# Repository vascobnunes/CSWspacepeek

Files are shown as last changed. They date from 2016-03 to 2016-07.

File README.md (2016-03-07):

# CSWspacepeek

A ideia consiste em construir um balão atmosférico com uma payload que permita filmar toda a sequência de ascenção e queda do balão, com principal foco na obtenção de imagens da superfície terrestre a partir do limiar do espaço, tendo o logotipo da critical em primeiro plano. 
Como objectivos secundários, tentar-se-iam recolher medições telemétricas, atmosféricas e geográficas da viagem.

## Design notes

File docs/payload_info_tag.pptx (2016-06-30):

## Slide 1

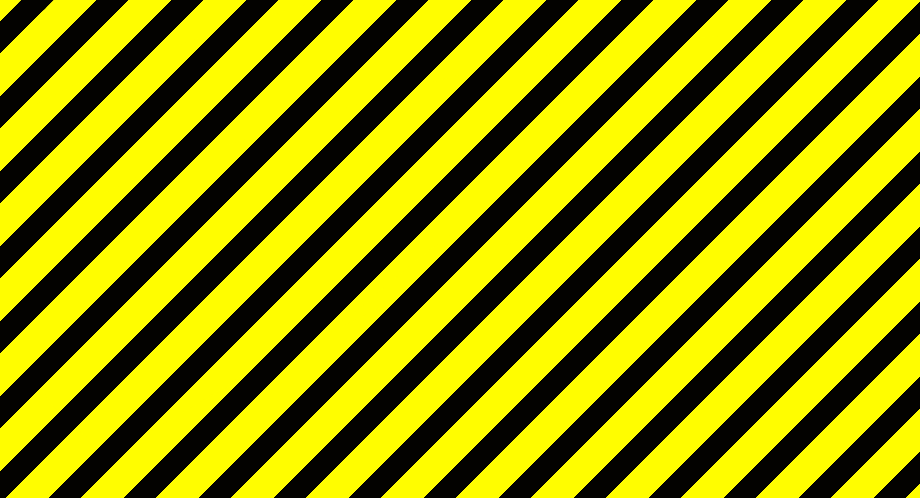
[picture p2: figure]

MEDIÇÕES METEOROLÓGICAS

SE ENCONTRAR POR FAVOR:
NÃO ABRA A CAIXA

CONTACTE:
spacepeek@gmail.com
+351 91 321 50 55
RECOMPENSA PELA DEVOLUÇÃO

CAIXA E CONTEÚDOS NÃO PERIGOSOS

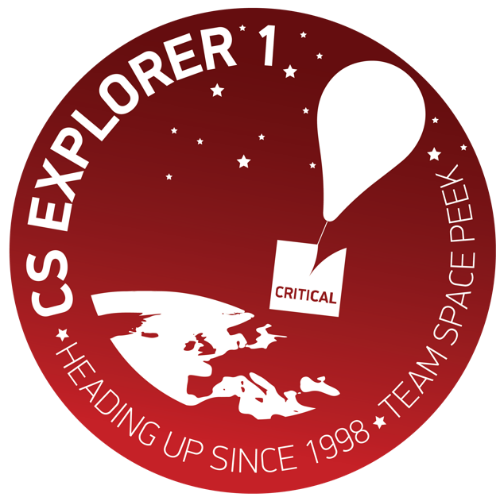
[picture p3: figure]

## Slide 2

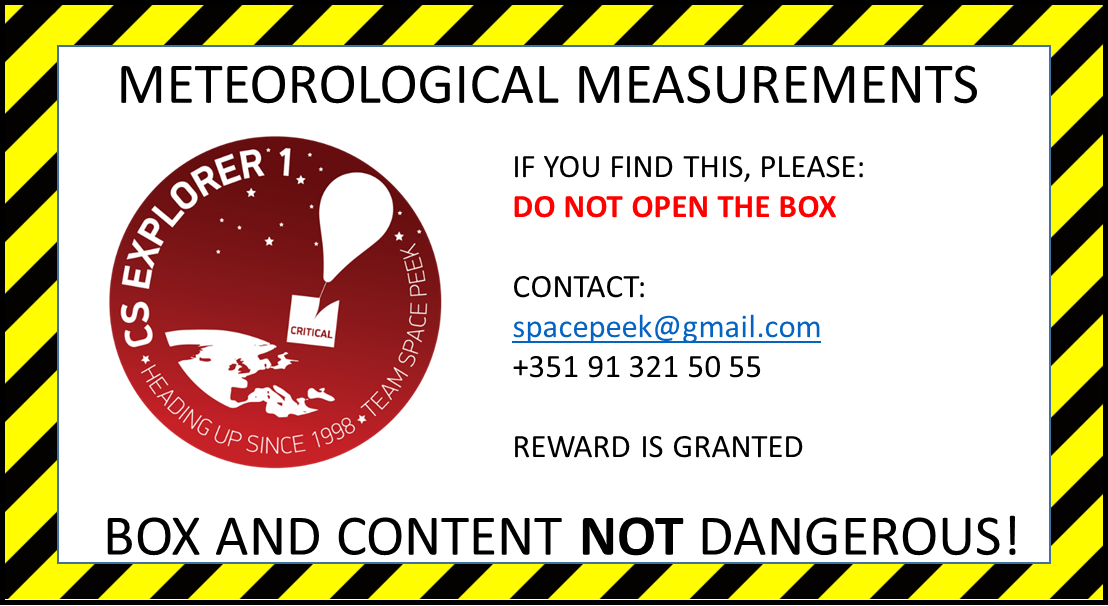
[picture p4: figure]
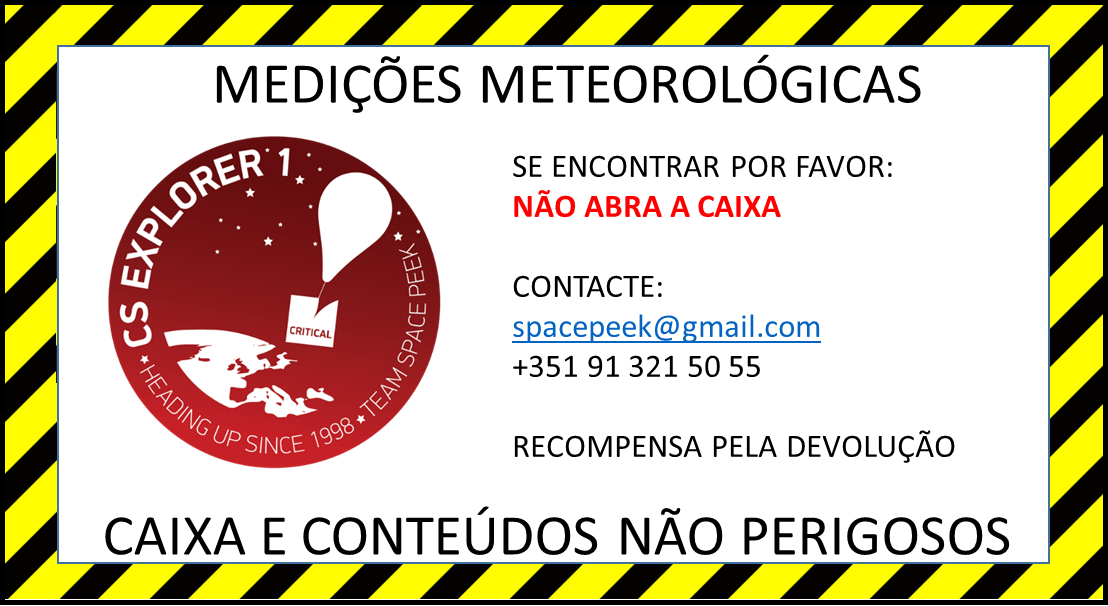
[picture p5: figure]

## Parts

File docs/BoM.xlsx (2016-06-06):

Category | Item # | Item Description | Amount | Provider / website | Unit Price | Total Price | Procurement priority | Notes for procurement
Flight hardware | ~~1~~ | ~~Balão testes (100g)~~ | ~~0~~ | ~~http://randomsolutions.co.uk/Random_Aerospace/Balloons.html~~ | ~~34.08 €~~ | ~~0.00 €~~ | Deprecated
 | 2 | Brand New, High Quality Balloon. 1000g Hwoyee HY-1000 (£46.95) | 1 | http://randomsolutions.co.uk/Random_Aerospace/Balloons.html | 59.67 € | 59.67 € | High | Items #2, #3, #26 and #27 can be ordered together
 | 3 | RocketMan Balloon Parachute - 3ft (£39.95) | 1 | http://randomsolutions.co.uk/Random_Aerospace/Parachutes.html | 50.78 € | 50.78 € | High | Items #2, #3, #26 and #27 can be ordered together
 | 26 | 1.0mm Braided Nylon Cord - Breaking strain approx. 22.5Kg (220N**). Weight approx. 0.6g per meter (£2.25) | 1 | http://randomsolutions.co.uk/Random_Aerospace/Stuff.html | 2.86 € | 2.86 € | High | Items #2, #3, #26 and #27 can be ordered together
 | 27 | 2.7L Polystyrene Payload Box (£7.95) | 1 | http://randomsolutions.co.uk/Random_Aerospace/Stuff.html | 10.11 € | 10.11 € | High | Items #2, #3, #26 and #27 can be ordered together
 | 4 | Hélio | 8 m3 | TBD | ? | ? | N/A
 | 5 | Duct tape | 1 rolo | TBD | ? | ? | N/A
 | 6 | Bocal Enchimento balão | 1 | 3D Printed, source TBD (estimated around 45€) | 45.00 € | 45.00 € | N/A
Payload | 7 | rPi 3 | 1 | http://pt.rs-online.com/web/p/kits-de-desarrollo-de-procesador-y-microcontrolador/8968660/ | 33.10 € | 33.10 € | Done | Items #7, #8 and #11 can be bought together
 | 8 | rPi 3 power supply | 1 | http://pt.rs-online.com/web/p/fuente-de-alimentacion-enchufable/9098135/?origin=PSF_430702|acc | 8.68 € | 8.68 € | Done | Items #7, #8 and #11 can be bought together
 | 9 | Cartão microSD Class10 32GB | 1 | https://www.worten.pt/32gb-micro-sd-class-10.html | 17.99 € | 17.99 € | Done
 | 10 | GrovePi | 1 | Fikalab | Ready | Ready | N/A
 | 11 | Raspberry Pi Camera board V2 8MP 1080p | 1 | http://pt.rs-online.com/web/p/modulos-de-video/9132664/?origin=PSF_437599|rel | 23.09 € | 23.09 € | Done | Items #7, #8 and #11 can be bought together
 | 12 | Habduino + Radiometrix MTX2 434Mhz + 144.800Mhz (Euro) Radiometrix HX1 | 1 | https://store.uputronics.com/index.php?route=product/product&path=62&product_id=57 | 183.53 € | 183.53 € | Done | Make sure to select options: "Radiometrix MTX2 434Mhz (+£31.44)" plus "144.800Mhz (Euro) Radiometrix HX1 (+£29.04)" Total price should be £144.47 (including VAT) Items #12 and #13 can be bought together
 | 13 | UHF/VHF Antenna for Habduino | 1 | https://store.uputronics.com/index.php?route=product/product&path=63&product_id=61 | 20.96 € | 20.96 € | Done | Items #12 and #13 can be bought together
 | 14 | Grove sensor suite | 1 | Fikalab | Ready | Ready | N/A
 | 15 | Battery pack for rPi | 2 | Fikalab | Ready | Ready | N/A
 | ~~16~~ | ~~Redundant GPS (SPOT)~~ | ~~0~~ | ~~http://www.findmespot.eu/shop/index.php?main_page=product_info&cPath=5&products_id=32 ~~ | ~~125.00 €~~ | ~~0.00 €~~ | Not needed
 | 17 | Logótipo da CSW em 3D | 1 | TBD | ? | ? | N/A
 | 25 | ArduBerry SKU : A-000000-01422 | 1 | http://www.generationrobots.com/en/401804-arduberry.html | 48.06 € | 48.06 € | High
Ground station | 18 | SDR USB-Dongle | 1 | http://www.nooelec.com/store/sdr/sdr-receivers/nesdr-mini-rtl2832-r820t.html | Ready | Ready | N/A
 | ~~19~~ | ~~UHF Antenna (TBC)~~ | ~~0~~ | ~~http://pt.farnell.com/lprs/yagi-434a/antenna-yagi-7-element-434mhz/dp/2096215~~ | ~~40.71 €~~ | ~~0.00 €~~ | N/A
 | ~~20~~ | ~~Cabo/adaptator para ligar antena ao USB-Dongle (MCX FEMALE TO SMA MALE) (TBC)~~ | ~~0~~ | ~~http://mauser.pt/catalog/product_info.php?products_id=66009 ~~ | ~~12.48 €~~ | ~~0.00 €~~ | N/A
 | 21 | Laptop | 1 | N/A | Ready | Ready | N/A
 | 22 | VHF/UHF handheld radio | 1 | https://www.amazon.co.uk/BaoFeng-UV-5RE-Dual-Radio-Earpiece/dp/B00EYYVEH6?s=electronics | 29.19 € | 29.19 € | Done
 | 23 | Mobilinkd TNC2.1 (APRS support) | 1 | https://store.mobilinkd.com/products/mobilinkd-tnc2-1 | 57.44 € | 57.44 € | Done | Items #23 and #24 can be bought together
 | 24 | TNC Cable for Kenwood, Wouxun, Baofeng | 1 | https://store.mobilinkd.com/products/kenwood-wouxun-baofeng-tnc-cable | 8.80 € | 8.80 € | Done | Items #23 and #24 can be bought together
 |  |  |  |  |  | 599.26 €

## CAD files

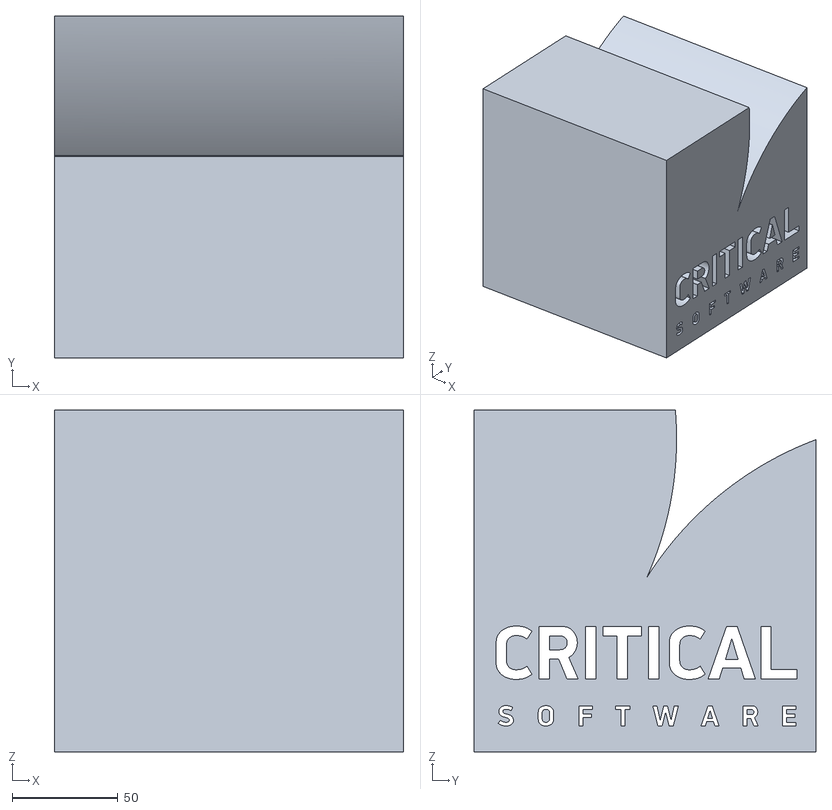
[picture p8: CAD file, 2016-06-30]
docs/logo3d/VAZADO.stl
165.0 x 161.7 x 161.7

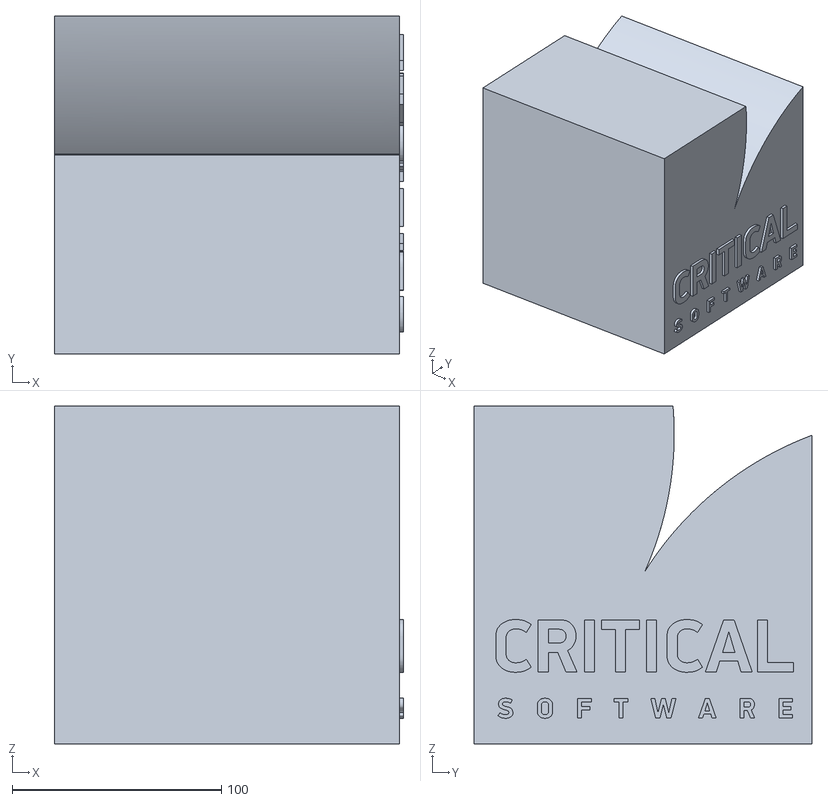
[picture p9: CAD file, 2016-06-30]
docs/logo3d/RELEVO.stl
167.0 x 161.7 x 161.7

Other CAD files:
docs/logo3d/RELEVO2.stl
docs/logo3d/VAZADO2.stl

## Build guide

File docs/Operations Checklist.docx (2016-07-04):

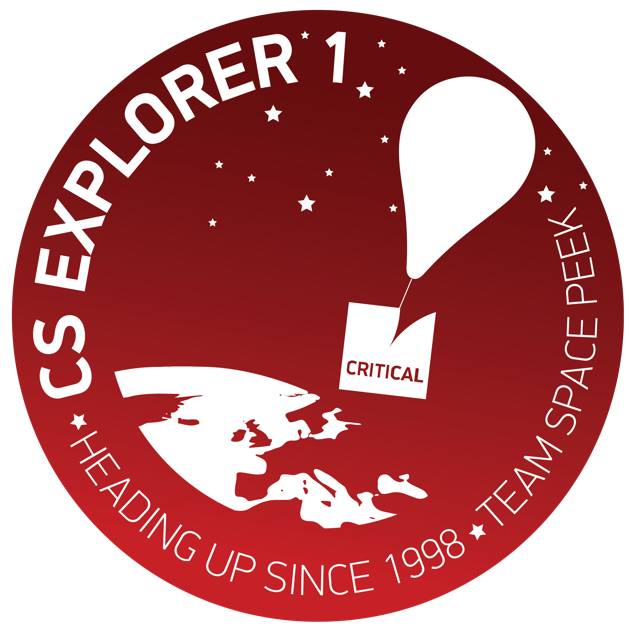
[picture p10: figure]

CSEXPLORER1 OPERATIONS CHECKLISTS

SPACE PEEK

2016

Run GO/NO GO checklist

- T-2h predictor indicates recovery location >10km inland - GO
- T-2h predictor indicates recovery location >10km off urban - GO
- Pre Fly Day Checklist checked - GO

1 - Pre Fly Day Checklist

- Inform Flight control T – 25h
  - Run predictions and prepare Pre Flight Report
  - Send email to flight control T – 24h
- Check flight computer, Sensors and Calibrate T-17h
  - Charge power bank
  - Update calibration values for sensors
  - Take trial images. Download images to computer and check them.
  - Take sensor trial measurements. Download to computer and check them.
  - Check communications – 144.8
  - Check communications – 434Mhz
- Packing tools T-16h
  - Wire cutter, scissors, knife, pen, paper, torch
- Packing payload Sealed T-15h
  - Check payload materials
  - Payload box closed and sealed
  - Payload box labels
  - Weight payload
- Packing Balloon and Filling Equipment T-14h
  - Check balloon materials
  - Check tank and filling equipment.
  - Tank, pressure reducer, hose, fill tube.
  - Weight to check balloon fill state.
- Packing Tracking Equipment T-13h
  - Check Ground Stations materials.
  - Car power switch source.
- Recovery vehicle(s)
  - Fueled up

2 - Pre Fly Checklist

- Run GO/NO GO checklist
- Inform Flight control T-60min
  - Generate new prediction and check for deviations.
  - Call flight control and confirm launch and time (tel:218553314).
- Start Ground Station Computer T-50min
  - Power up and power computer via car power switch source.
  - Create local hotspot and connect computer to it.
  - Connect FUNcube Dongle via USB cable to lower USB.
  - Start DSP Radio, Fldigi and Flight Control Centre. Check frequency setting.
  - Start Flight Control Centre and check if working.
- Start Up HAB T-30min
  - New batteries in SPOT
  - New batteries in habduino
  - Set scripts to autostart on boot
  - Set Date/Time on Raspberry PI before starting scripts
  - Lay out protecting blanket
  - Connect battery to flight computer (turn on the payload)
  - Check signal received in ground station
  - Check successful transmission
  - Lay out rigging lines and parachute to check for damage
  - Check surrounding area to be free of obstacles
- Filling Balloon T-20min
  - Put gloves on.
  - Unpack and attach filling equipment to tanks. Remember check weights.
  - Open tank valve and check flow. Close tank valve.
  - Unpack balloon and put over filling tube. Fix balloon with cable ties and tape.
  - Start inflating balloon till nearly lift of check weights. Consider wind!
  - Connect rigging line with solid nodes.
  - Disconnect balloon from filling tube and close balloon end tight.
- Launch Balloon T-0min
  - Check aerial to not be bend.
  - Check transmission and camera to record.
  - Watch out for obstacles.
  - Let it go.

3 - Post Fly Checklist

- On site recovery
  - Call flight control (and confirm touchdown or loss)
  - Photograph payload box before touching
  - Recover payload box
  - Open payload box
  - Stop image capture
  - Power down flight control computer
- In Base
  - Copy logged data to computer
  - Copy images to computer
  - Backup data

4 - Materials / tools

- Duct tape
- Payload #1
  - Rpi3
  - Grovepi
  - Sensor Temp/hum
  - Sensor Magnet/accel
  - Power bank
  - Power cable
  - Camera #1
  - Habduino
  - Pilhas habduino
  - Arduberry
  - Antena GPS
  - Antena 70cm
  - Antena 2m
  - Camera #2
  - Beacon transmiter
  - Régua
  - Logo 3D
- Ballon
  - Abraçadeiras
  - Bocal de enchimento
  - Mangueira
  - Garrafas de Hélio
  - Luvas
  - Cobertura
- Ground Station #1
  - PC do Hélio + Carregador
  - Conversor para isqueiro do carro
  - HackRF
  - Antena portátil do Miguel
  - Fichas SMA fêmea-fêmea
  - Fichas SMA fêmea-PL fêmea
  - HUB internet 3G Miguel
  - YAGI antenna
- Ground Station #2
  - PC EEC
  - Rádio A-linco
  - Antena portátil grande
  - Cabo áudio
  - Cabos ligação isqueiro
  - Carregador de Ipad
  - Ipad do freitas
  - Rato
- Mobil station
  - Rádio Boafeng
  - Cabo áudio
  - TNC Bluetooth
  - Telemóvel Freitas
  - Carregador de telemóvel

SPACE PEEK – CSEXPLORER 1

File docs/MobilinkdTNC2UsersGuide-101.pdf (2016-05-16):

TNC2 User Guide

## Mobilinkd TNC2 User Guide

Thank you for purchasing your new Mobilinkd TNC2 Battery-powered Bluetooth TNC.
This TNC is designed to suit all aspects of the Amateur Radio community. It is ready to plug in and go with easy to use and intuitive configuration software, and it is completely open for experimentation. The schematics are published and all software used in the TNC is open source and available online.

Overview
This guide will introduce you to the key features of the TNC, its connectors, switches and indicator LEDs. Most of this manual illustrates the configuration and operation of the TNC using an Android device and Android software. However, the TNC will work with any operating system and software that can talk to a KISS TNC over Bluetooth SPP (Serial Port Profile).

KISS TNC
The TNC2 is a KISS TNC, which means that it is purely a modem and not really a terminal node controller. A more accurate description of the TNC2 and all KISS devices is a KISS modem. The TNC2 does not manipulate the packets it receives in any manner. It cannot, by itself, digipeat (relay) packets or do any store and forward operations associated with an intelligent TNC. This is an important point that can be a source of some confusion. A KISS TNC simply encodes and decodes digital information as audio that can be transmitted over the air by a radio on a voice channel.

The Mobilinkd TNC System
The Mobilinkd TNC System is comprised of three physical components: A radio, the Mobilinkd TNC, and a computer, tablet or smart phone that supports Bluetooth SPP (serial port profile). This currently excludes all Apple iOS devices because Apple does not support SPP in iOS. The TNC connects to the radio with a cable and talks to the smartphone or computer via Bluetooth connection.

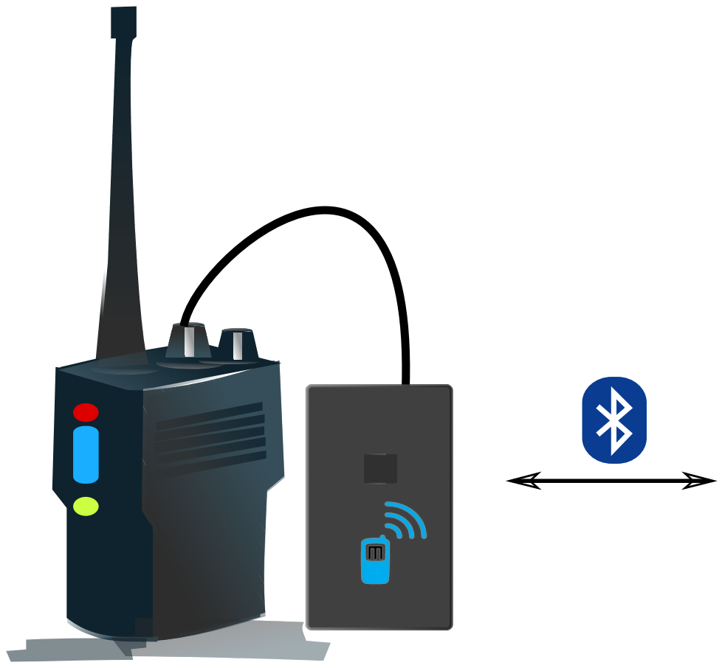
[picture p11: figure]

TNC Switches, Connectors and Indicators
The Mobilinkd TNC2 has one switch, two connectors and two indicators. Each of these is shown in the image and described below.

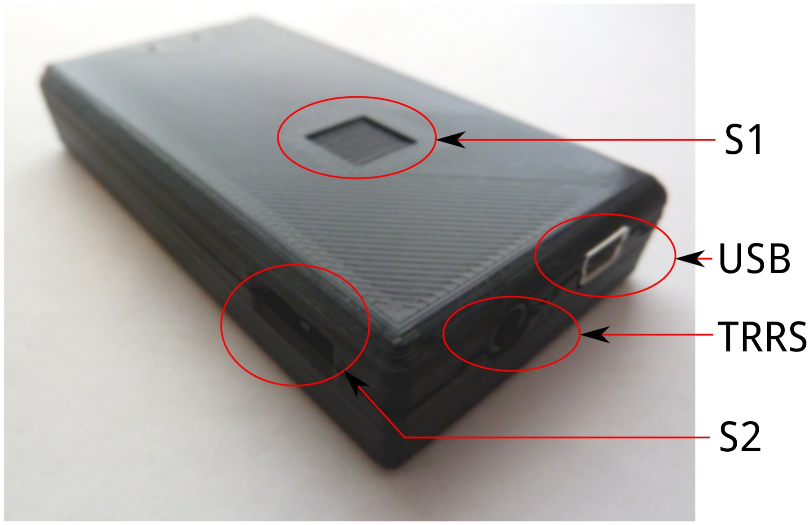
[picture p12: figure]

S1 – Power button. Press briefly to turn on. Power/BT LED will flash. Press briefly to turn off. The power/Bluetooth LED will turn off.

S2 does not exist on the TNC2.

USB – Mini-USB connector for charging/power. (Cannot be used for data.)

TRRS – 3.5mm TRRS audio connector for Radio.
1. Tip = Speaker (audio input to TNC)
2. Ring 1 = PTT (with S2 to right)
3. Ring 2 = Mic (and PTT with S2 to left)
4. Sleeve = GND/Common

Blue LED – The power/Bluetooth indicator. Flashes fast when pairing and slow when paired. Red LED – Charge indicator. On when connected to USB and charging, otherwise off.

Before First Use
The battery will not be fully charged when you receive the TNC. It is always best to plug in a mini-USB cable and charge the battery before first use. When the Red LED turns off, the battery is charged. The battery will typically last for 48 hours of continuous use when paired to another device. The battery drains much faster when powered on but not paired. The TNC consumes about 6x as much power when unpaired than when paired.

TNC Cable
Now is also a good time to put the ferrite bead on the TNC cable. All TNC2s come with a ferrite bead. The ferrite bead must be installed on the cable between the TNC and radio to prevent RF from the radio from interfering with the operation of the TNC.
For thinner HT cables, pass the cable twice through the core of the bead by forming a loop with the cable and pulling it tight before clipping the ferrite bead closed. This may take some force to get the cable to fit, but it is important, especially if you are running a Baofeng radio. These radios can emit a lot of RF energy through the speaker-mic connector, affecting the performance of the TNC.

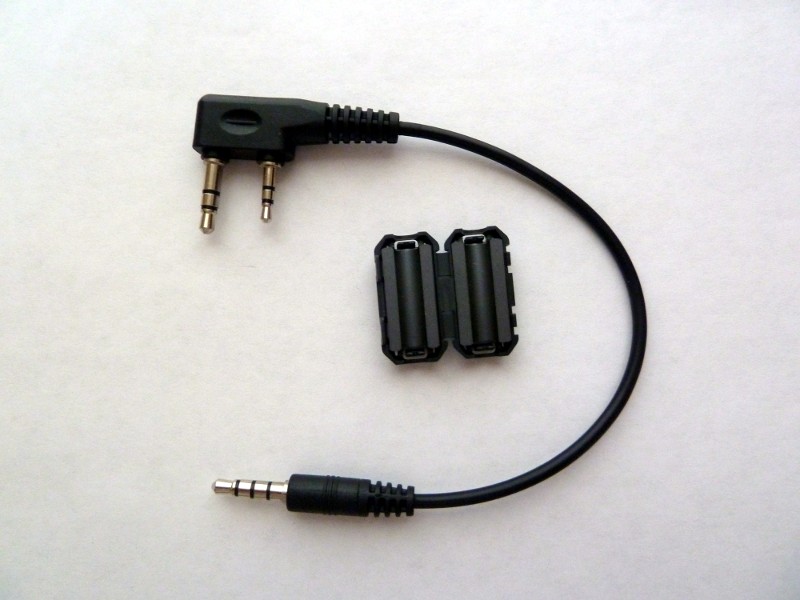
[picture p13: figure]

Radio Settings

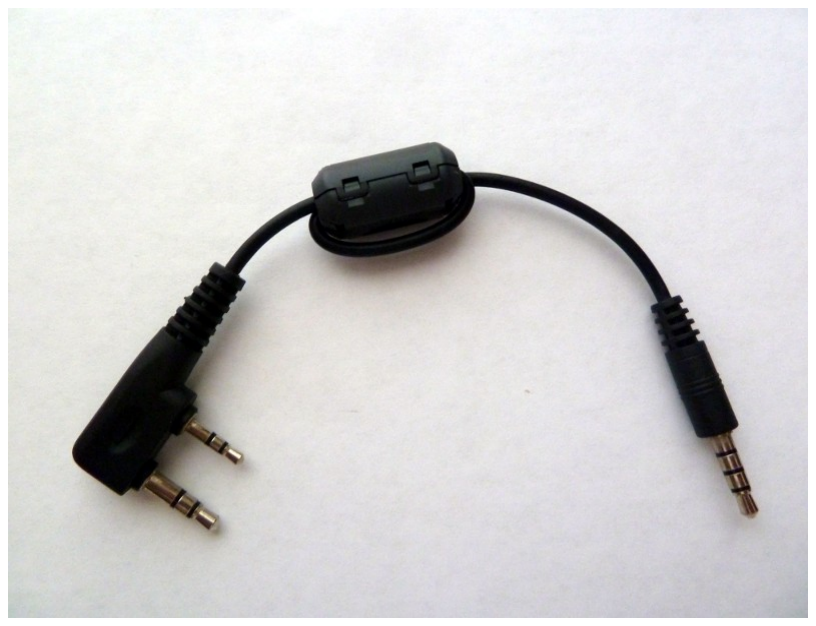
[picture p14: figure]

Each radio is different, so having a comprehensive list of optimal settings in a document like this is not possible. However, it is important to understand what radio settings impact the performance of the TNC and its ability to decode packets.
One of the more important aspect of how well the TNC will decode packets is how quickly the radio can open its squelch when a signal is present. If the radio cannot open its squelch fast enough, the start of each packet will be truncated and the TNC will be unable to decode any packets.
Troubleshooting Tip: If you are having trouble decoding packets, set the radio's squelch setting to 0 (open squelch) and turn the on the TNC's DCD setting. If the TNC can decode packets with the squelch open, the radio is opening its squelch too slowly.
The most important setting to disable on virtually all HTs is the “Battery Saver” option. This puts the radio to sleep for short periods of time. You will never notice for voice communication, but for many radios this will prevent most packets from being decoded. If you have an inexpensive Chinese radio (Baofeng, Wouxun, and many others) with a “Dual Receive” feature, this must also be disabled. This essentially operates the receiver as a scanner, switching the receiver between two frequencies.

Connecting the TNC
Connect the TNC to the HT with both the TNC and the radio turned off.
Plug the straight 3.5mm connector into the TNC. If your
radio's Speaker/Mic connector also uses a single 3.5mm
audio connector, the elbow connector goes to the radio.

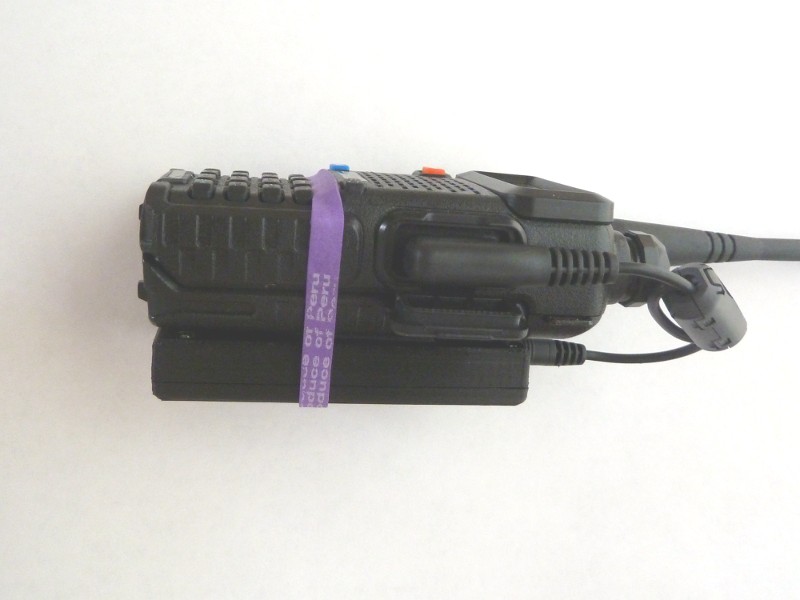
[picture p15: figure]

Plug the radio connector (these styles vary) into the radio's Speaker/Mic connector.

Connecting/Pairing
Detailed instructions for pairing the TNC on Android are below.
1. Press S1 briefly to turn on TNC. The blue LED will flash rapidly.
2. Ensure Bluetooth is enabled on other device.
3. On other device, scan for Bluetooth devices. You should see “Mobilinkd TNC2”.
4. Connect to “Mobilinkd TNC2”. Use password “1234” when prompted.

Pairing with an Android Device
1. Install the Mobilinkd Configuration App for Android (https://play.google.com/store/apps/details?id=com.mobilinkd.tncconfig) (available on Google Play.)
2. Open the Mobilinkd app.
3. Press S1 briefly to turn on TNC. The blue LED will flash rapidly.
4. Open the app menu and select “Bluetooth settings”
5. In the Bluetooth settings menu, select “Search for devices”
6. When you see “Mobilinkd TNC2”, select it.
7. Use password “1234” when prompted for a password. You should notice that the blue LED on the TNC starts flashing more slowly.
8. Hit the back button to go back the the Mobilinkd app.

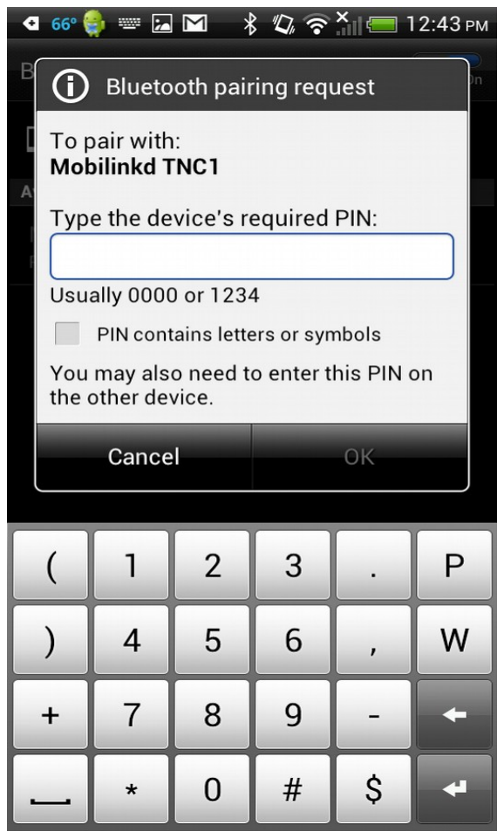
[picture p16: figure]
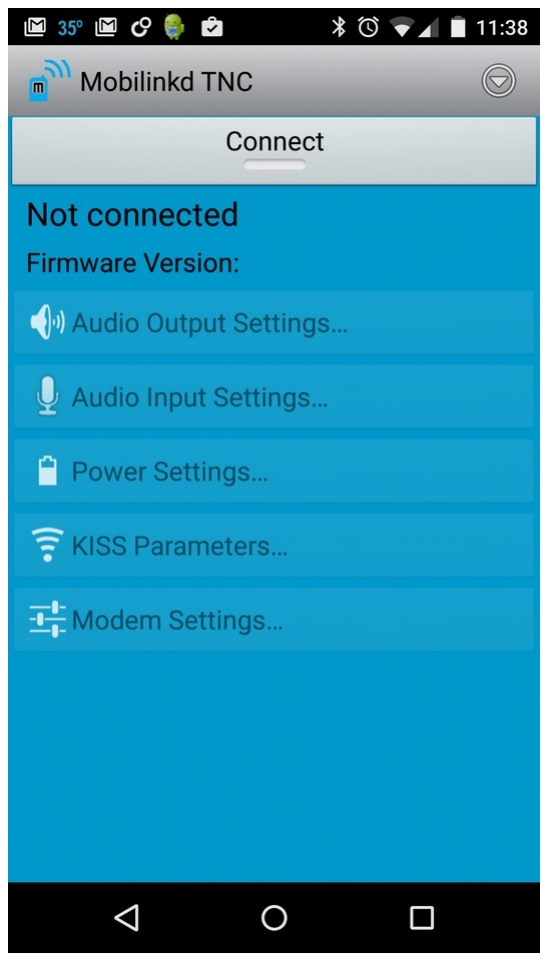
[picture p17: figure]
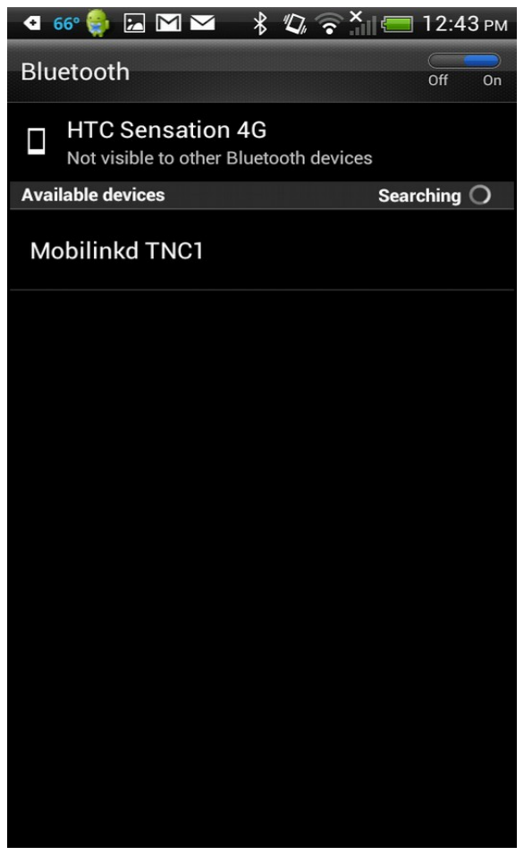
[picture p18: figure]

Configuring the TNC
This section assumes that you have followed the “Pairing with an Android Device” section above and have the Mobilinkd TNC config application running. The TNC and radio should be connected, the TNC should be on, and the radio should still be off at this point.
1. Push the “Connect” button to connect the Mobilinkd TNC Bluetooth device. You will see the device name and firmware version displayed.

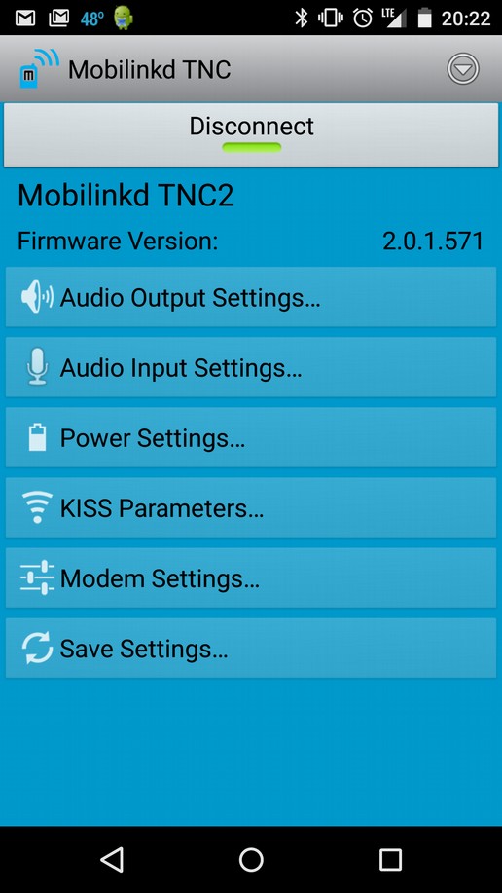
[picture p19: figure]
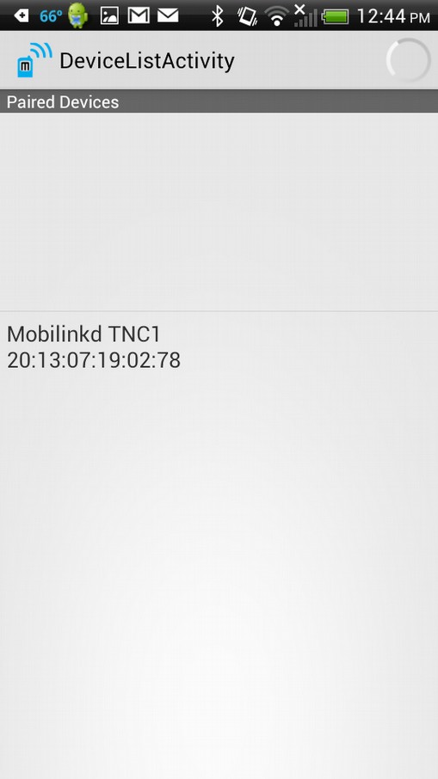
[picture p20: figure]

The image on the right shows the main menu for the Mobilinkd Config app. This menu is the starting point to launch the various screens shown in the documentation below. When you are done with a certain activity, press the “Close” button to go back to this screen.

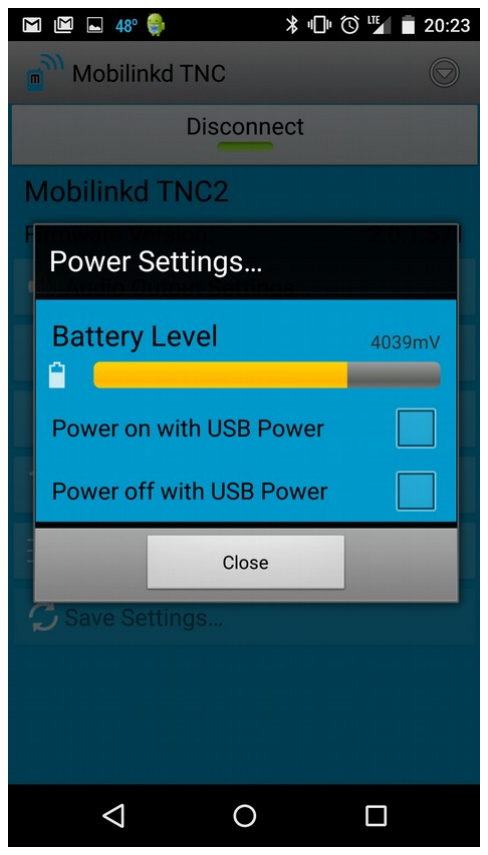
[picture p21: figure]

Configuring the Power Settings
You can check the battery level and configure the power settings from the “Power Settings” dialog. The TNC2 is fully charged when it reads approximately 4.2V (4200mV). The nominal battery voltage is 3.7V. Avoid operating the TNC below 3.4V, otherwise erratic behavior may occur.
The TNC may be configured to automatically turn itself on when USB power is present, and automatically turn itself off when USB power is not present. This is often desirable when using the TNC in a vehicle. These settings are controlled independent of one another.
- To power on when USB power is present, select the “Power on with USB Power” option.
- To power off when USB power is removed, select the “Power off with USB Power” option.

Configuring Receive (RX/Input) Volume
The radio's volume level must be properly adjusted for optimal packet decoding. Press the “Audio Input Settings” button.
1. Turn the radio on.
2. The Attenutate Input options should be selected. If not, turn it on.*
3. Hold open the squelch on the radio either by pressing the radio's monitor button or by setting the squelch level to 0. You should see the volume meter activate.

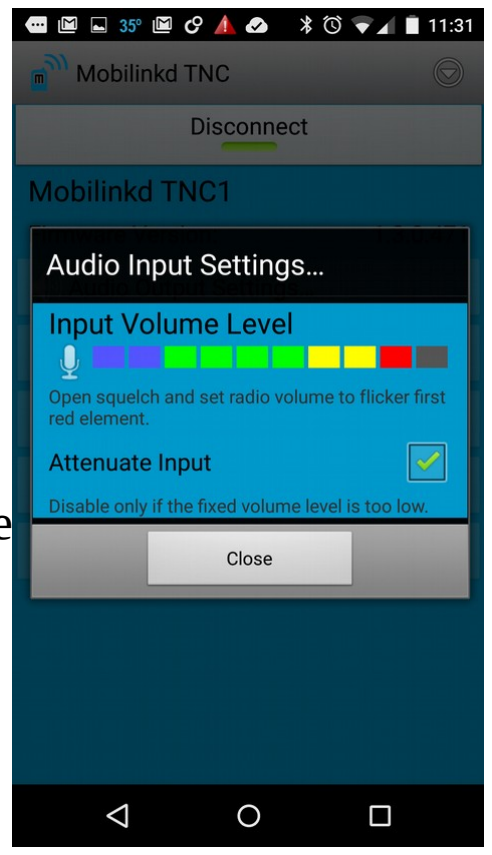
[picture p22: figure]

4. Adjust the volume on the radio until the volume meter lights up 8 of the 10 indicators and the 9th indicator (first red indicator) occasionally flickers.**
5. If you cannot turn up the volume high enough on the radio to light up 8
of the indicators, turn Attenutate Input off.
6. Press the Close button to return to the main menu.

* In general it is best to have input attenuation turned on. This often not possible with fixed volume mobile or base stations.
** If your radio uses the volume knob for on/off, it may be helpful to mark on the radio and knob with the optimal volume setting so it can be set quickly after turning on the radio.

Configuring Transmit and (TX/Output) Volume
Select the “Audio Output Settings” button on the main menu to open the audio output settings.
Modern ham radios use two different signaling methods for the Push-to-Talk (PTT) signal, which causes the radio to transmit.
Most base stations, mobile rigs (anything that uses a MiniDIN-6 data connector) and any radios with a Kenwood-style connector use a separate PTT line to trigger PTT. This form of PTT signaling is called “simplex” since there is one signal on the line.
Many HTs (Yaesu, Icom, Alinco and others) use the Mic+ line for both audio and PTT signaling. This form of PTT signaling is called “multiplex” since there are multiple signals on the same line.
If you don't know which one yours uses, trial and error works to figure it out.

Transmit (TX/Output) Volume

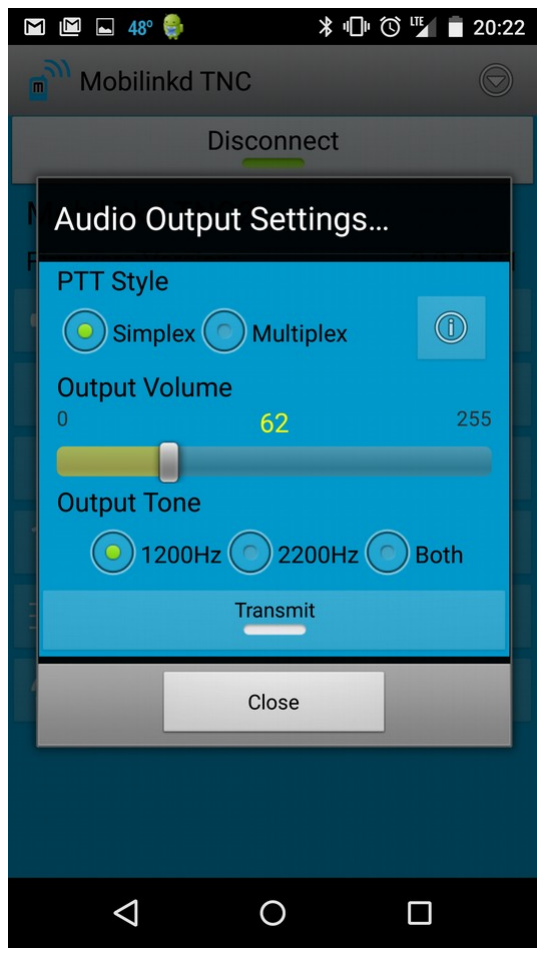
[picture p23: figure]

Configuring the transmit volume requires a second radio and, without expensive monitoring equipment, will be a bit subjective. The default volume level (128) is a very good starting point. It may not be necessary to adjust the volume level at all.
This exercise is best done with the TNC/radio connected to a dummy load or at low power. Both radios should be set for simplex on an open frequency so as not to interfere with others. Do not adjust the radio's output volume while tuned to the primary APRS frequency.
To adjust the radio volume, select 2200Hz tone button, then press the Transmit button.
While monitoring the tone on the second radio, adjust the Output Volume slider until you do not hear the volume increasing any more. Then back off the volume by 10%.
You cannot adjust the output volume unless the Transmit button is selected. This is by design, to prevent accidentally changing the output volume.
Troubleshooting: If you do not hear the any audio or the TX indicator on your radio does not light up, verify that the PTT Style selected above is correct. Disable TX, then change the PTT Style selection and try again.

Configuring the KISS Parameters
These parameters are best left at their default values: TX Delay – 33
Persistence – 64
Slot Time – 10
TX Tail – 2
TX Delay represents the amount of time in 10s of milliseconds that the TNC will key the radio and transmit the preamble before sending the packet.
Persistence is part of the CSMA backoff represents the odds (out of 256) that the TNC will transmit within its slot time when no carrier is detected.
Slot Time is also part the the CSMA protocol; it is the delay in 10s of
milliseconds that the TNC waits before checking whether it can transmit.

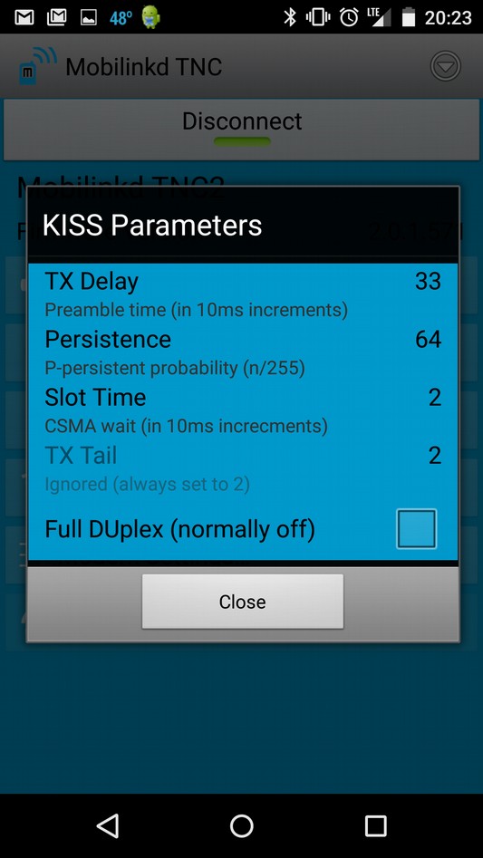
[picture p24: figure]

TX Tail is the amount of time in 10s of milliseconds the TNC keys the transmitter after the packet is sent. It must always be 2.
Full Duplex – ignore carrier detect and the CSMA parameters and trasmit without waiting for a clear channel. The assumption is that while running duplex, the TX channel is always clear.
Please see http://www.ka9q.net/papers/kiss.html for a more in-depth discussion of these KISS parameters.

Modem Settings
The other TNC options that can be set are:
DCD – whether to use the Data Carrier Detect feature of the TNC rather than just audio energy detected. DCD is required when running with an open squelch. Please enable this setting. It should be on by default.
BT Connection Tracking – When enabled, the TNC tracks the state of the Bluetooth connection and discards any packets received while the Bluetooth

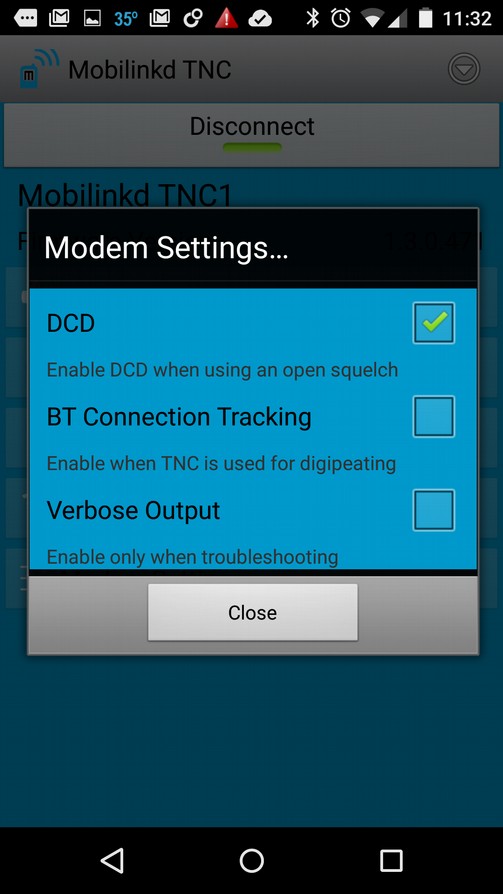
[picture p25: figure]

connection is down. Otherwise packets are queued and downloaded when the the connection is re-established. This must be enabled when operating a digipeater or iGate in order to prevent old, stale packets from being digipeated (relayed) or entering APRS-IS.
Verbose Output – send out of band detailed packet diagnostics. These are displayed in the APRSdroid log. This may be helpful when diagnosing receive or packet decode issues. It should normally be turned off because it reduces the TNCs ability to decode certain packets. (The time spent reporting diagnostics is time the TNC cannot spend decoding packets.)

Firmware Update
Mobilinkd releases firmware updates for the TNC from time to time. This allows us to provide enhancements and bug fixes for the TNC, increasing the performance and value of the TNC over time. Firmware updates are typically announced via our web page, Yahoo message board and via Twitter.
To upload a new firmware image to the TNC, make sure than no app is currently connected to the TNC. Exit the Mobilinkd Configuration app and make sure your APRS software not in “Tracking” mode. Disconnect the TNC from the radio. Then just follow the link to the new firmware image. The configuration app will automatically start and ask if you would like to install the new firmware image. Only install firmware for the correct model of TNC. Installing firmware for a different model almost certainly will render the TNC inoperable.

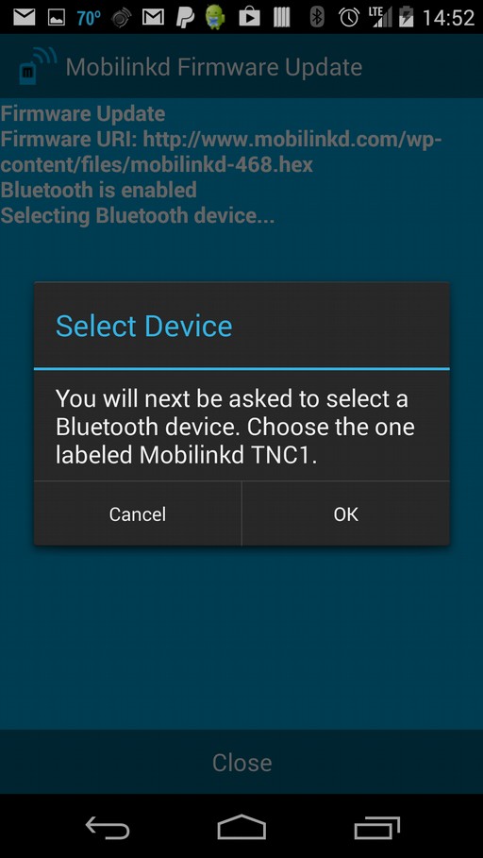
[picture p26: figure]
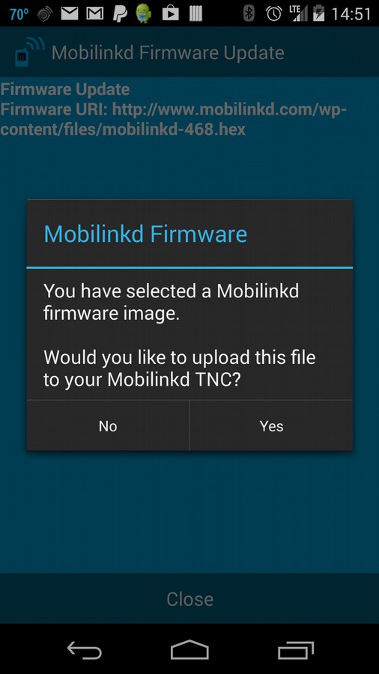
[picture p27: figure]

Firmware Update (cont)
Once connected, you will be asked to confirm that you want to upload the image. It is important that you do allow the firmware update to complete before navigating away from the Mobilinkd Config app.
You will see the firmware first being written and then being verified.

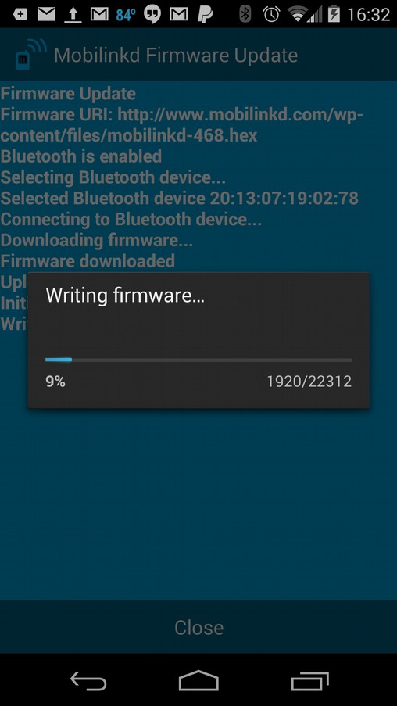
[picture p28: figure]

Once the firmware is verified, the TNC will reboot and the new firmware will be loaded.
You may need to reset the configuration of the TNC once this is complete. The TNC2 retains the previous settings by default.

Recommendations For Use with APRSdroid
This assumes that you know have followed the “Connecting/Pairing” and “Configuring the TNC” steps above. This is a good first-time setup and
should be customized to your needs once you are familiar with APRS and
APRSdroid.

You are encouraged to download the APRSdroid software from Google Play. (https://play.google.com/store/apps/details?id=org.aprsdroid.app) You can also find the software at http://aprsdroid.org/. Detailed APRSdroid configuration documentation can be found on the APRSdroid GitHub site: https://github.com/ge0rg/aprsdroid/wiki/Settings.

Before starting, turn the radio off to avoid accidentally transmitting bad APRS data.

1. Ensure the TNC is on and paired with the Android device. Make sure the Mobilinkd Config app is disconnected and that you have exited the app.
2. Start APRSdroid.
3. Go into Menu|More|Preferences
1. Set your SSID. SSID 7 is common for hand-held radios.
2. Set your APRS symbol. If you don't know which one to use, choose /[ for now. That will put a “jogger” symbol on the map for your position. See also http://www.aprs.net/vm/DOS/SYMBOLS.HTM
3. Personalize the comment field.
4. Under “Location Source”, select “Periodic GPS/Network Position”.
5. Under “Location Settings|GPS Precision”, select “Low”. If this device connects to a mobile phone network, select “Use network position”.
6. Under “Connection Protocol”, select “Bluetooth TNC”.
7. Under “Connection Preferences|TNC Bluetooth Device”, select “Mobilinkd TNC2”
8. Under “Connection Preferences|APRS digi path”, enter “WIDE1-1,WIDE2-1”
9. Enable “Connection Logging”
4. Return to the main screen.
5. There are three views: Hub, Map, and Log. Ensure you are in Log view.
6. Select “Start Tracking”.
7. The blue LED should start blinking more slowly (two brief blinks every 2 seconds).
8. You should see a green line in the APRSdroid log where it sent a position report to the TNC.

If you receive an error “java.io.IOException” in the log when trying to connect, verify that the TNC is on and that it is flashing fast (no established connection). If the TNC is flashing slowly with a double-pulse, it is connected to another app.

Sending your First Packet
1. Turn on the Radio and ensure its volume level is set properly.
2. Tune the radio to your primary APRS (http://info.aprs.net/index.php?title=Frequencies#Primary_VHF_Networks) frequency. (http://info.aprs.net/index.php?title=Frequencies#Primary_VHF_Networks)
3. Press S1 briefly to turn on the TNC. The blue LED will flash rapidly.
4. Start APRSdroid and select “Start Tracking”. The LED will flash slowly when connected. This will immediately beacon your position.

When testing the TNC, it is best to ensure that a digipeater is nearby or that you have another APRS/packet radio to test with. A hand-held radio will typically need line of sight to a digipeater within 3-5km (2-3 miles) in order to have the signal digipeated.

Listen to the audio on the local APRS frequency. If at least some of the signals are clear and free from static or audio distortion, the TNC should be able to decode those APRS packets.

Some adjustment of the audio level may be required to get optimum packet decoding. Every radio model is different and the volume levels necessary may vary considerably. Even after following RX audio configuration steps above, the volume level may need to be adjusted to get the optimal performance out of the system.

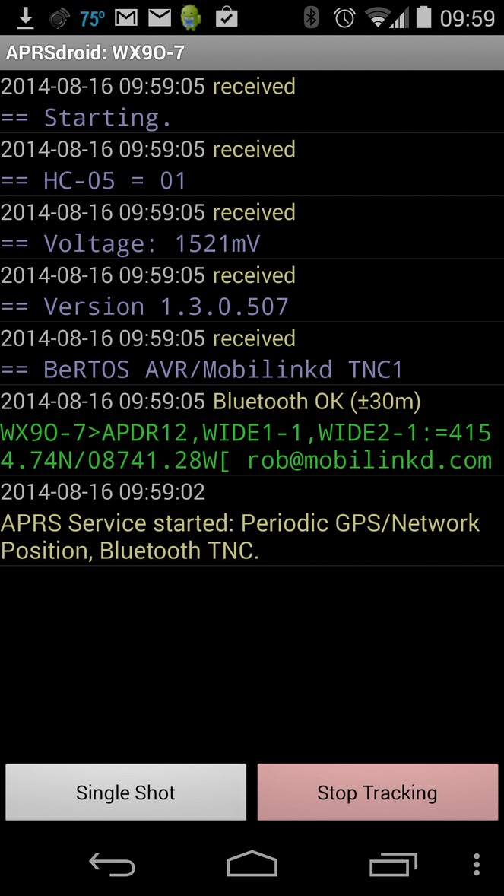
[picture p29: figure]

The APRSdroid Log
When the Mobilinkd TNC powers on, it writes out diagnostic
information that will be captured by APRSdroid in its log. This includes things like the firmware version and the battery voltage. When troubleshooting problems it is often very helpful to verify the current firmware version and the battery level. To get this information, follow these steps.
1. Press “Stop Tracking” in APRSdroid.
2. Turn the TNC off, then turn the TNC on.
3. Press “Start Tracking” in APRSdroid.

Troubleshooting

Cannot Connect to TNC
- Make sure no other applications are currently connected to the TNC. Only one application can connect to the TNC at a time. The TNC should be flashing quickly (about 2Hz). You may need to reboot your device to get it to release the Bluetooth connection. When using APRSdroid, make sure that you press “Stop Tracking” before attempting to use the Mobilinkd Config app. Conversely, when using the Mobilinkd Config app, make sure you “Disconnect” before you attempt to use APRSdroid.
- Turn off WiFi on the device. Some Android devices do not operate well when both Bluetooth and WiFi are enabled. Both use the same 2.4GHz ISM band for communication and, if not managed properly, can interfere with one another.
- Power cycle the TNC.
- Re-pair with the TNC.
- Plug the TNC into USB power.

Cannot Communicate with TNC
- If the squelch on the radio is open and DCD is not selected, the TNC can appear to stop responding. It is, in fact, waiting to send a packet. Disconnect the TNC from the radio. This will allow the TNC to clear its buffer. After the TNC has been disconnected from the radio, start the Mobilinkd Config app and enable DCD. The TNC will function normally.

TNC Will Not Decode Packets
- Verify that the TNC's battery is fully charged. Plug the TNC into USB power and see if the problem persists.
- Verify that strong TNC packets can heard on the channel.
- Enable the DCD setting and open the squelch on the radio.
- Verify that the TNC can detect the audio and the RX volume is adjusted properly.

TNC Will Only Decode Packets with Squelch Open
- Adjust the radio's settings to open squelch faster.
- Try a different make/model radio.

No RX Audio Detected
- Ensure that the cable is firmly plugged into the radio and into the TNC.
- Verify connectivity on the cable.
- Verify that the TNC boots properly by checking the APRSdroid log.

TNC Will Not Transmit
- Verify that it is not an improper APRS software configuration by using the Mobilinkd Configuration App to send tones. (See Configuring Transmit Volume above.)
- Ensure that the cable is firmly plugged into the radio and into the TNC.
- Verify that PTT Style is set properly for the radio.
- Verify cable continuity.
- Verify that the TNC boots properly by checking the APRSdroid log.

Packets Not Digipeated
- Make sure packets are being transmitted.
- Make sure packets can be decoded.
- Make sure digipeater is in range.
- Get closer to the digipeater.

Transmitted Packets Not Decoded
- Lower the transmit volume. (See Configuring Transmit Volume above.)
- Verify the radio is on the correct frequency.
- Try a different receiver and TNC.
- Increase the TX Delay KISS Parameter. (Values above 50 are not recommended and may reduce APRS network bandwidth in congested areas.)

Not Showing Up in APRS-IS (or on aprs.fi)
- Make sure an iGate is in range of your radio.
- Move closer to the iGate.

TNC Reboots When Transmitting
Do not operate the TNC if it is rebooting when the radio transmits. This is typically indicates that strong RF fields are affecting the TNC's circuitry. This may damage the TNC.
- Verify that the TNC cable has a ferrite bead attached.
- Check the TNC cable, the radio, and radio antenna for damage.
- Re-position the TNC and cable away from the radio's antenna.
- Try another radio.

No Start-up Diagnostics in APRSdroid Logs
- Plug the TNC into USB power.
- Verify that either the radio's squelch is normally close d or DCD is enabled.
- Re-flash the firmware. (See Firmware Update above.)

Software Customization
The TNC has a AVR109-compatible bootloader. Firmware can be updated over the Bluetooth connection using the Mobilinkd Config app for Android or the open source program “avrdude”.
avrdude -P <COM PORT> -c avr109 -p m328p -b 115200 -U <FIRMWARE>

For the more adventurous types, the TNC has a 6-pin ISP connector. The ISP is programmed using a 6-pin pogo-pin adapter (such as Digi-Key (http://www.digikey.com/product-detail/en/823-22-006-10-004101/ED8179-06-ND/1147045) ED8179-06-ND) (http://www.digikey.com/product-detail/en/823-22-006-10-004101/ED8179-06-ND/1147045) that is pressed onto the 6 pin connector. Or a standard 2.54mm 6-pin header can be soldered in place for programming.
The code running on the TNC is based on KISS TNC code contributed to BeRTOS by Robin Gilks G8ECJ. The code has been modified for the hardware. The code is available from GitHub. See http://www.mobilinkd.com/ and follow the links to GitHub. The firmware for the TNC2 is on the “tnc2” branch.
This firmware is released under the GPL. Hacking (AKA “voiding your warranty”) is highly encouraged.
https://github.com/g8ecj/bertos/tree/g8ecj/hdlc – original version https://github.com/mobilinkd/tnc1 – latest firmware (the TNC2 code is on the “tnc2” branch)

Acknowledgments
APRSdroid is written and maintained by Georg Lukas, DO1GL.
APRS is a registered trademark of Bob Bruninga, WB4APR.

Copyright
Copyright 2015 Mobilinkd LLC. All Rights Reserved.

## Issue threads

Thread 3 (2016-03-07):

Criar listagem de hardware necessário

vascobnunes, 2016-03-07:

vascobnunes, 2016-03-14:
O @rafaelluissantos vai enviar uma lista para a comissão do FikaLab. A lista está aqui:
https://dl.dropboxusercontent.com/u/18901524/CSW%E2%80%99s%20space%20peek%20-%20hardware.png

rafaelluissantos, 2016-03-14:
E-mail sent.

vascobnunes, 2016-03-15:
resposta do andré - fikalab:

"Acho que têm aí uma ideia muito interessante. É mesmo esse o tipo de ideias que aqui o pessoal do FikaLab queria ver. :-D

Aqui vão algumas alternativas de material semelhante que temos já aqui disponível no FikaLab, e que podem já começar a experimentar, se quiserem:

Alternativa 1:
https://drive.google.com/open?id=0B69oP6B9IdlkRHdSOUhXOTdiUEE

- LinkIt One: http://www.seeedstudio.com/depot/LinkIt-ONE-p-2017.html
     - inclui GPS, GPRS, e SD card
- LinkSprite Camera: https://www.sparkfun.com/products/11610
     - resolução máxima 640x480 :-(

Com esta alternativa, dava para controlar o disparo das fotografias, por
exemplo uma por segundo, para ser ao mesmo tempo que os dados da posição
GPS, e dava para gravar tudo sincronizado no cartão SD.

Alternativa 2:
https://drive.google.com/open?id=0B69oP6B9IdlkNGxuQzVBQU9OUG8

- Arch GPRS V2: http://www.seeedstudio.com/depot/Arch-GPRS-V2-p-2026.html
     - inclui GPRS e SD card
- GPS: http://www.seeedstudio.com/depot/Grove-GPS-p-959.html
- LinkSprite Camera: https://www.sparkfun.com/products/11610
     - resolução máxima 640x480 :-(

Esta alternativa é muito semelhante à anterior, é mais uma questão de
preferência pessoal em relação ao processador.

E temos também aqui um painel solar, que vos poderá ser útil:
https://drive.google.com/open?id=0B69oP6B9IdlkN0VwWjRKdmZDNFE

Mas o custo da vossa lista de material, exactamente como está, parece-me
bastante razoável, e acho que não haverá problema em adquirí-la
integralmente, se preferírem."

vascobnunes, 2016-03-15:
Diria que neste momento temos a seguinte listagem (@rafaelluissantos - dás tu continuidade a isto com o pessoal do Fikalab?):

Fase 1 - Payload

 - (OK) Linkit One com GPS, GPRS e SD card - http://www.seeedstudio.com/depot/LinkIt-ONE-p-2017.html
 - (OK) Painel solar - https://drive.google.com/open?id=0B69oP6B9IdlkN0VwWjRKdmZDNFE
 - (ORDER) Camera compatível com LinkitOne com resolução HD e melhor que 30fps;
 - (TO CONFIRM) Battery e battery case;
 - (TO CONFIRM) Temperature sensor compatível com o LinkIT One;
 - (TO CONFIRM) Humidity sensor compatível com o LinkIT One;
 - (TO CONFIRM) Accelerometer compatível com o LinkIT One;
 - (TO CONFIRM) Gyroscope compatível com o LinkIT One;
 - (TO CONFIRM) Breadboard compatível com o LinkIT One;
 - (GET) Caixa para tudo isto;
 - (GET) Material isolador;

rafaelluissantos, 2016-03-15:
Vamos ver o que diz o André. Alguma coisa posto aqui.

rafaelluissantos, 2016-03-18:
UPDATE:

"
Boa tarde André,

Segue então a listagem do material requisitio e levantado para a CSW Lx:
- 1x LinkitOne;
- 1x Grove IMU;
- 1x Grove Temperature & Humidity.

Vamos iniciar os testes.
Obrigado.
Rafael Santos
"

Let's partyyy

rafaelluissantos, 2016-03-18:
MISSING, to acquire after first tests:

Fase 1 - Payload

**(TO BE CHECKED BY FIKA) **Painel solar - https://drive.google.com/open?id=0B69oP6B9IdlkN0VwWjRKdmZDNFE

**(WE MUST FIND ONE SUITABLE) **Camera compatível com LinkitOne com resolução HD e melhor que 30fps;

**(ORDER) **Battery e battery case;

**(IS THIS NECESSARY?) **Breadboard compatível com o LinkIT One;

**(GET, WHICH ONE?) **Caixa para tudo isto;

**(GET, WHICH ONE? AND HOW TO USE?) **Material isolador;

vascobnunes, 2016-03-18:
A caixa é arranjar esferovite e duct tape e fazer uma. Isto é fácil.
Material isolador, temos de mandar vir. Está na lista original http://cdn.instructables.com/F1R/BF7O/HQVQ00C9/F1RBF7OHQVQ00C9.LARGE.jpg

rafaelluissantos, 2016-03-18:
Ya, mas se queremos que o FIka adquira temos que enviar links e orçamento mais pomposo feito. Depois vemos isso, temos é que começar a mexer com isto.

vascobnunes, 2016-03-22:
UPDATE:
Fase 1 - Payload

    (OK) Linkit One com GPS, GPRS e SD card - http://www.seeedstudio.com/depot/LinkIt-ONE-p-2017.html
    (OK) Painel solar - https://drive.google.com/open?id=0B69oP6B9IdlkN0VwWjRKdmZDNFE
    (ORDER) Camera compatível com LinkitOne com resolução HD e melhor que 30fps;
    (ORDER) Battery e battery case;
    (OK) Temperature sensor compatível com o LinkIT One;
    (OK) Humidity sensor compatível com o LinkIT One;
    (OK) Accelerometer compatível com o LinkIT One;
    (OK) Gyroscope compatível com o LinkIT One;
    (ORDER) Breadboard compatível com o LinkIT One;
    (GET) Caixa para tudo isto;
    (GET) Material isolador;

Closed 2016-05-11.

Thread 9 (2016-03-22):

Instalar Arduino IDE e compatibilidade com o LinkitOne

vascobnunes, 2016-03-22:

framioco, 2016-03-22:
Downloaded Arduino 1.6.8 for ARM (https://github.com/NicoHood/Arduino/releases) and Java 8 (http://www.rpiblog.com/2014/03/installing-oracle-jdk-8-on-raspberry-pi.html); Also upgraded the OS since some necessary packages were a bit outdated. Still we have an error trying to execute arduino:
/home/pi/arduino-1.6.8/lib/libastylej.so: /usr/lib/arm-linux-gnueabihf/libstdc++.so.6: version `GLIBCXX_3.4.20' not found (required by /home/pi/arduino-1.6.8/lib/libastylej.so)
Cannot load native library /home/pi/arduino-1.6.8/lib/libastylej.so
The program has terminated!

framioco, 2016-03-22:
Updating OS from debian wheezy to jessie - that will fix this problem and bring more updated packages to the system overall. Hope everything goes fine! Will report here shortly after the upgrade is done.

framioco, 2016-03-23:
OS upgraded to debian jessie which brings the libstdc++6 version up to date (to the required version by Arduino IDE). The IDE now runs (haven't tried to connect to the Linkit board though).

vascobnunes, 2016-03-23:
Nice! Thanks @framioco

framioco, 2016-03-23:
Mediatek LinkIt board installed via Board Manager in the Arduino IDE.

Closed 2016-05-20.

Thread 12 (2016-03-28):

Fill authorization forms

vascobnunes, 2016-03-28:
Pelo que percebi do que o Hugo e o Hélio investigaram, temos:

 - pedido à ANAC
 - pedido à NAV
 - pedido ao estado maior das forças armadas - captação de imagens aéreas
 - pedido ao estado maior das forças armadas - divulgação de imagens aéreas

Closed 2016-07-05.

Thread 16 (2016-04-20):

rPi grove sensor - IMU 10DOF

vascobnunes, 2016-04-20:
Connect and collect data

vascobnunes, 2016-05-23:
Grove - IMU 10DOF is a combination of Grove - IMU 9DOF and Grove - Barometer Sensor (BMP180)
BMP180 is already working with script data_collection.py

Closed 2016-06-06.

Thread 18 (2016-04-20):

rPi camera: HD video + stills

vascobnunes, 2016-04-20:
Should have some logic to collect several small videos allong the mission and retrieve and send ocasional still frames from the videos.

framioco, 2016-05-23:
First commit on this in a562cb4

Closed 2016-06-06.

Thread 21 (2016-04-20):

Investigate redundant location/comunication system

vascobnunes, 2016-04-20:

jlnfreitas, 2016-04-25:
Could use something similar to what Balua is using in their latest launch:
[Map tracking through spot findme of Balua Launch from 25/04/2016](http://share.findmespot.com/shared/faces/viewspots.jsp?glId=0scHf6UmOhIOAIsIPUtx9GcSECJy90SMV)

According to their [site](http://www.amrad.pt/balao-balua-amradamsat-ct-lars-atualizacaoii/), they actually use 3 different types of communication reporting systems:

_"1- Tracker com emissor APRS e GPS desbloqueado a funcionar em 144,8 MHz- Callsign  CS5PBAL  e CS5PBA-11 em APRS,
2- Spot the comunicações por satélite com recetor de GPS e indicação de posição de 5 em 5 minutos – emissor para satélite em 14 GHz e receção em internet;
3- Beacon para localização do payload no terreno em 434,485 MHz  (transmite bip -bip)"_

**1. APRS ("Automatic Packet Reporting System")**
With a GPS + APRS one can report the position using the 144.8MHz frequency.
It requires a radio amateur license. Our colleague [António Alves](https://wise.critical.pt/wiseweb/users/UserDetails.action?login=aalves&companyId=1) should have one.
We have 3 options: use a COTS tracker, build our own tracker or assemble an Arduino or Pi based Kit. The 3 options are reviewed below:

a) We can either use a COTS equipment such as [Tracksoar](https://www.tracksoar.com/) ( incudes temperature, pressure, and humidity sensors, GPS receiver and antenna, costs 165USD and weights 45grams).

b) We can [build one](http://makezine.com/projects/hab-aprs-tracker/) (more difficult)

c) Or we can assemble an Arduino based or as Raspberry Pi based kit such as the [Habduino](http://www.habduino.org/) (sold as a kit by [uptronics](https://store.uputronics.com/index.php?route=product/product&path=62&product_id=57) at a cost of 145€) or the [Pi in the Sky](http://www.pi-in-the-sky.com/) sold as a kit by [Uptronics as well](https://store.uputronics.com/index.php?route=product/product&path=62&product_id=52) at a cost of 216.15€)
The [Pi in the Ski manual](http://www.pi-in-the-sky.com/data/uploads/pits-manual.pdf) provides detailed information on how to assemble the board, connect it to an existing Raspberry Pi, setup and test the reception.
The reception of the signal can be made using an RTL SDR dongle [similar to the one I have to track ADS-B signals](http://www.nooelec.com/store/sdr/sdr-receivers/nesdr-mini-rtl2832-r820t.html), but with a decent TBD antenna.

**2. Spot Satcom**
The spot satcom tracker requires a SPOT equipment with a satcom data plan (weight < 100g, cost around 150€ - equipment + USB power cable + data plan)
They use a  [Spot satellite tracker](http://www.findmespot.eu/shop/index.php?main_page=product_info&cPath=5&products_id=32) which costs around 102€ (125€ with VAT)

plus a [data service plan](http://www.findmespot.eu/en/index.php?cid=131) which costs 10€ a month.

**3. 434,485MHz beacon**
As for the 434,485MHz beacon, it can actually be added as an extra option to the APRS transmitter, both to the [Habduino kit](https://store.uputronics.com/index.php?route=product/product&path=62&product_id=57) and to the [Pi in the Sky kit](https://store.uputronics.com/index.php?route=product/product&path=62&product_id=52)

Finally a list of different tracking options can be found [here](https://community.balloonchallenge.org/t/current-gps-tracker-products/668)

Closed 2016-05-20.

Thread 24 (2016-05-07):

Migrar github para gitlab

O2F, 2016-05-07:
http://doc.gitlab.com/ee/workflow/importing/import_projects_from_github.html
- Vai ser necessário a tua participação devido a credenciais no ato da migração
- Se já tivermos o projecto em gitlab, possivelmente será mais facil recrear o mesmo dado que em leitura diagonal vi que o import e feito no ato da criação do projeto no gitlab.

framioco, 2016-05-09:
Qual é o endereço do gitlab da CSW?

vascobnunes, 2016-05-09:
https://gitlab.critical.pt

O gitlab é p a critical toda, mas depois há equipas às quais se podem associar projectos. Há já uma equipa do fikalab por isso faz sentido criar o projecto dentro da equipa.

Closed 2017-11-28.

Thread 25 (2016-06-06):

Update BOM with launcher material

vascobnunes, 2016-06-06:
http://randomsolutions.co.uk/Random_Aerospace/Stuff.html
1.0mm Braided Nylon Cord - Breaking strain approx. 22.5Kg (220N**).  Weight approx. 0.6g per meter

http://randomsolutions.co.uk/Random_Aerospace/Balloons.html
Brand New, High Quality Balloon.  1000g Hwoyee HY-1000

http://randomsolutions.co.uk/Random_Aerospace/Parachutes.html
RocketMan Balloon Parachute  - 3ft

Closed 2016-06-08.

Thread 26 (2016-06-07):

TypeError: 'int' object is not iterable

vascobnunes, 2016-06-07:
Traceback (most recent call last):
  File "cswxp1_sensors.py", line 85, in <module>
    [temp,hum]=dht(dht_sensor_port,1)
TypeError: 'int' object is not iterable

vascobnunes, 2016-06-08:
os sensores grove não ligam quando está conectado o power unit MoPi_v3 com a alimentação por transformador.

Closed 2016-06-08.

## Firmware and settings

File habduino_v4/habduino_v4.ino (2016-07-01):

/*
 HABDuino Tracker
 http://www.habduino.org
 (c) Anthony Stirk M0UPU 
 
 March 2015 Version 4.0.0
 
 This is for the Version 4 Habduino Hardware.
 
 Credits :
 
 Interrupt Driven RTTY Code : Evolved from Rob Harrison's RTTY Code.
 Thanks to :  http://www.engblaze.com/microcontroller-tutorial-avr-and-arduino-timer-interrupts/
 http://gammon.com.au/power
 
 Suggestion to lock variables when making the telemetry string & Compare match register calculation from Phil Heron.
 APRS Code mainly by Phil Heron MI0VIM
 
 GPS Code modified from jonsowman and Joey flight computer CUSF
 https://github.com/cuspaceflight/joey-m/tree/master/firmware
 
 Thanks to :
 
 Phil Heron
 James Coxon
 Dave Akerman
 
 The UKHAS Community http://ukhas.org.uk
 
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
 See <http://www.gnu.org/licenses/>.
 
 The Habduino kit is supplied as is with no guarantees of performance or operation. Although the HABDuino 
 is designed for short-term Near Space operation, the conditions may exceed the specification of individual 
 components which may fail to operate correctly because of low temperatures or pressures of increased 
 radiation levels. We have no control over the effectiveness of your payload design especially the 
 temperature and electromagnetic conditions  within, thus we make no warrnaty express or implied as to
 the ability of our products to operate to any degree of effectiveness when used in your application.
 
 If you decide to use this product under a balloon it’s your responsibility to ensure you comply with the 
 local legislation and laws regarding meteorological balloon launching and radio transmission in the air. 
 
 The Radiometrix MTX2 434Mhz is NOT license exempt in the United States of America and does need a radio
 amateur license.  Use of APRS requires a radio amateur license in all countries and a number of countries 
 don’t permit the airborne use of APRS under any circumstances.  
 The Habduino cannot do APRS without an addon Radiometrix HX1 module.
 
 The hardware design & code for Habduino is released under a Creative Commons License 3.0 Attribution-ShareAlike License :
 See : http://creativecommons.org/licenses/by-sa/3.0/
 It is YOUR responsibility to ensure this kit is used safely please review the safety section.
 
 The latest code is available here : https://github.com/HABduino/HABduino
 
 
 */

/* BITS YOU WANT TO AMEND */

#define MTX2_FREQ 434.485 // format 434.XXX  
char callsign[9] = "CT1EUS";  // MAX 9 CHARACTERS!!

/* BELOW HERE YOU PROBABLY DON'T WANT TO BE CHANGING STUFF */

#include <util/crc16.h>
#include <avr/io.h>
#include <avr/interrupt.h>
#include <avr/pgmspace.h>
#include <OneWire.h>
#include <DallasTemperature.h>
#include <SoftwareSerial.h>
#include "ax25modem.h"
static const uint8_t PROGMEM _sine_table[] = {
#include "sine_table.h"
};
#define ASCII 7          // ASCII 7 or 8
#define STOPBITS 2       // Either 1 or 2
#define TXDELAY 0        // Delay between sentence TX's
#define RTTY_BAUD 50     // RTTY Baud rate (Recommended = 50)
#define LED_WARN 9
#define LED_OK 8
#define BATTERY_ADC A0
//#define MTX2_SHIFT 425        
//#define MTX2_OFFSET 0          // 0-100 Slightly adjusts the frequency by increasing the PWM 
#define MTX2_TXD 4
#define MTX2_ENABLE 7


#define HX1_ENABLE 6
#define HX1_TXD 3
#define GPS_ON 2
#define POWERSAVING
#define ONE_WIRE_BUS 5
#define ONE_SECOND F_CPU / 1024 / 16


#define BAUD_RATE      (1200)
#define TABLE_SIZE     (512)
#define PREAMBLE_BYTES (50)
#define REST_BYTES     (5)

#define PLAYBACK_RATE    (F_CPU / 256)
#define SAMPLES_PER_BAUD (PLAYBACK_RATE / BAUD_RATE)
#define PHASE_DELTA_1200 (((TABLE_SIZE * 1200L) << 7) / PLAYBACK_RATE)
#define PHASE_DELTA_2200 (((TABLE_SIZE * 2200L) << 7) / PLAYBACK_RATE)
#define PHASE_DELTA_XOR  (PHASE_DELTA_1200 ^ PHASE_DELTA_2200)

SoftwareSerial MTX2_EN(12, MTX2_ENABLE); // RX, TX
OneWire oneWire(ONE_WIRE_BUS);
DallasTemperature sensors(&oneWire);

volatile int txstatus=1;
volatile int txstringlength=0;
volatile char txc;
volatile int txi;
volatile int txj;
volatile int count=1;
volatile boolean lockvariables = 0;
volatile static uint8_t *_txbuf = 0;
volatile static uint8_t  _txlen = 0;

int errorstatus=0;
/* Error Status Bit Level Field :
 Bit 0 = GPS Error Condition Noted Switch to Max Performance Mode
 Bit 1 = GPS Error Condition Noted Cold Boot GPS
 Bit 2 = DS18B20 temp sensor status 0 = OK 1 = Fault
 Bit 3 = Current Dynamic Model 0 = Flight 1 = Pedestrian
 Bit 4 = PSM Status 0 = PSM On 1 = PSM Off                   
 Bit 5 = Lock 0 = GPS Locked 1= Not Locked
 
 So error 8 means the everything is fine just the GPS is in pedestrian mode. 
 Below 1000 meters the code puts the GPS in the more accurate pedestrian mode. 
 Above 1000 meters it switches to dynamic model 6 i.e flight mode and turns the LED's off for additional power saving. 
 So as an example error code 40 = 101000 means GPS not locked and in pedestrian mode. 
 */

char txstring[100];
uint8_t buf[60]; 
uint8_t lock =0, sats = 0, hour = 0, minute = 0, second = 0;
uint8_t oldhour = 0, oldminute = 0, oldsecond = 0;
int GPSerror = 0,navmode = 0,psm_status = 0,lat_int=0,lon_int=0,tempsensors,temperature1=0,temperature2=0;
int32_t lat = 0, lon = 0, alt = 0, maxalt = 0, lat_dec = 0, lon_dec =0 ,tslf=0, last_alt=0;
unsigned long currentMillis;
long previousMillis = 0;
int batteryadc_v,battvaverage=0,aprstxstatus=0; 
int32_t battvsmooth[5] ;
int aprs_tx_status = 0, aprs_attempts = 0;
unsigned long startTime;
char comment[6]={' ', ' ', ' ', ' ', ' ', '\0'};


void setup()  { 
  pinMode(MTX2_TXD, OUTPUT);
  pinMode(LED_WARN, OUTPUT);
  pinMode(HX1_ENABLE, OUTPUT);
  pinMode(LED_OK,OUTPUT);
  pinMode(MTX2_ENABLE, OUTPUT);
  pinMode(GPS_ON, OUTPUT);
  pinMode(BATTERY_ADC, INPUT);
  blinkled(6);
  setMTX2Frequency();
  Serial.begin(9600);
  digitalWrite(MTX2_ENABLE,HIGH);
  blinkled(5);
  digitalWrite(GPS_ON,HIGH);
  blinkled(4);
  resetGPS();
  blinkled(3);

#ifndef APRS
  TCCR2B = TCCR2B & 0b11111000 | 1; // Sets fast PWM on pin 11
#endif

#ifdef APRS
  ax25_init();
#endif

  blinkled(2);
  setupGPS();
  blinkled(1);
  initialise_interrupt();
  sensors.begin();
  tempsensors=sensors.getDeviceCount();
} 

void loop()   {
  oldhour=hour;
  oldminute=minute;
  oldsecond=second;
  gps_check_nav();

  if(lock!=3) // Blink LED to indicate no lock
  {
    errorstatus |=(1 << 5);  // Set bit 5 (Lock 0 = GPS Locked 1= Not Locked)
  }
  else
  {
    errorstatus &= ~(1 << 5); // Unset bit 5 (Lock 0 = GPS Locked 1= Not Locked)
  }
  checkDynamicModel();

#ifdef APRS 
  if(sats>=4){
    if (aprs_tx_status==0)
    {
      startTime=millis();
      aprs_tx_status=1;
    }
    if(millis() - startTime > (APRS_TX_INTERVAL*60000)) {
      aprs_tx_status=0;
      send_APRS();
      last_alt = alt;
      aprs_attempts++;
    }
  }  
#endif


#ifdef POWERSAVING
  if((lock==3) && (psm_status==0) && (sats>=5) &&((errorstatus & (1 << 0))==0)&&((errorstatus & (1 << 1))==0)) // Check we aren't in an error condition
  {
    setGPS_PowerSaveMode();
    wait(1000);
    psm_status=1;
    errorstatus &= ~(1 << 4); // Set Bit 4 Indicating PSM is on
  }
#endif
  if(!lockvariables) {

    prepare_data();
    if(alt>maxalt && sats >= 4)
    {
      maxalt=alt;
    }
  }
  if((oldhour==hour&&oldminute==minute&&oldsecond==second)||sats<=4) {
    tslf++;
  }
  else
  {
    tslf=0;
    errorstatus &= ~(1 << 0); // Unset bit 0 (Clear GPS Error Condition Noted Switch to Max Performance Mode)
    errorstatus &= ~(1 << 1); // Unset bit 1 (Clear GPS Error Condition Noted Cold Boot GPS)
  }
  if((tslf>10 && ((errorstatus & (1 << 0))==0)&&((errorstatus & (1 << 1))==0))) {
    setupGPS();
    wait(125);
    setGps_MaxPerformanceMode();
    wait(125);
    errorstatus |=(1 << 0); // Set Bit 1 (GPS Error Condition Noted Switch to Max Performance Mode)
    psm_status=0;
    errorstatus |=(1 << 4); // Set Bit 4 (Indicate PSM is disabled)
  }
  if(tslf>100 && ((errorstatus & (1 << 0))==1)&&((errorstatus & (1 << 1))==0)) {
    errorstatus |=(1 << 0); // Unset Bit 0 we've already tried that didn't work
    errorstatus |=(1 << 1); // Set bit 1 indicating we are cold booting the GPS
    Serial.flush();
    resetGPS();
    wait(125);
    setupGPS();
  }
}

void initialise_interrupt() 
{
  // initialize Timer1
  cli();          // disable global interrupts
  TCCR1A = 0;     // set entire TCCR1A register to 0
  TCCR1B = 0;     // same for TCCR1B
  OCR1A = F_CPU / 1024 / RTTY_BAUD - 1;  // set compare match register to desired timer count:
  TCCR1B |= (1 << WGM12);   // turn on CTC mode:
  // Set CS10 and CS12 bits for:
  TCCR1B |= (1 << CS10);
  TCCR1B |= (1 << CS12);
  // enable timer compare interrupt:
  TIMSK1 |= (1 << OCIE1A);
  sei();          // enable global interrupts
}

ISR(TIMER1_COMPA_vect)
{

  if(alt>1000 && sats >= 4)
  {
    digitalWrite(LED_WARN,LOW);  
    digitalWrite(LED_OK,LOW);  
  }
  else 
  {
    currentMillis = millis();
    if(currentMillis - previousMillis > ONE_SECOND) 
    {
      previousMillis = currentMillis;   
      if(errorstatus!=8)
      {
        digitalWrite(LED_WARN,!digitalRead(LED_WARN));
        digitalWrite(LED_OK,LOW);  
      }
      else 
      {
        digitalWrite(LED_OK, !digitalRead(LED_OK)); 
        digitalWrite(LED_WARN,LOW);    
      }
    }
  }

  switch(txstatus) {
  case 0: // This is the optional delay between transmissions.
    txj++;
    if(txj>(TXDELAY*RTTY_BAUD)) { 
      txj=0;
      txstatus=1;
    }
    break;
  case 1: // Initialise transmission
    if(alt>maxalt && sats >= 4)
    {
      maxalt=alt;
    }
    lockvariables=1;
#ifndef APRS
    if(tempsensors==1)
    {
      snprintf(txstring,100, "$$$$$%s,%i,%02d:%02d:%02d,%s%i.%06ld,%s%i.%06ld,%ld,%d,%i,%i,%02x",callsign,count, hour, minute, second,lat < 0 ? "-" : "",lat_int,lat_dec,lon < 0 ? "-" : "",lon_int,lon_dec, maxalt,sats,temperature1,battvaverage,errorstatus);
    }
    else
    {
      snprintf(txstring,100, "$$$$$%s,%i,%02d:%02d:%02d,%s%i.%06ld,%s%i.%06ld,%ld,%d,%i,%i,%i,%02x",callsign,count, hour, minute, second,lat < 0 ? "-" : "",lat_int,lat_dec,lon < 0 ? "-" : "",lon_int,lon_dec, maxalt,sats,temperature1,temperature2,battvaverage,errorstatus);
    }
#endif
#ifdef APRS
    if(tempsensors==1)
    {
      snprintf(txstring,100, "$$$$$%s,%i,%02d:%02d:%02d,%s%i.%06ld,%s%i.%06ld,%ld,%d,%i,%i,%i,%02x",callsign,count, hour, minute, second,lat < 0 ? "-" : "",lat_int,lat_dec,lon < 0 ? "-" : "",lon_int,lon_dec, maxalt,sats,temperature1,battvaverage,aprs_attempts,errorstatus);
    }
    else
    {
      snprintf(txstring,100, "$$$$$%s,%i,%02d:%02d:%02d,%s%i.%06ld,%s%i.%06ld,%ld,%d,%i,%i,%i,%i,%02x",callsign,count, hour, minute, second,lat < 0 ? "-" : "",lat_int,lat_dec,lon < 0 ? "-" : "",lon_int,lon_dec, maxalt,sats,temperature1,temperature2,battvaverage,aprs_attempts,errorstatus);
    }
#endif
    crccat(txstring);
    maxalt=0;
    lockvariables=0;
    txstringlength=strlen(txstring);
    txstatus=2;
    txj=0;
    break;

  case 2: // Grab a char and lets go transmit it. 
    if ( txj < txstringlength)
    {
      txc = txstring[txj];
      txj++;
      txstatus=3;
      rtty_txbit (0); // Start Bit;
      txi=0;
    }
    else 
    {
      txstatus=0; // Should be finished
      txj=0;
      count++;
    }
    break;
  case 3:
    if(txi<ASCII)
    {
      txi++;
      if (txc & 1) rtty_txbit(1); 
      else rtty_txbit(0);	
      txc = txc >> 1;
      break;
    }
    else 
    {
      rtty_txbit (1); // Stop Bit
      txstatus=4;
      txi=0;
      break;
    } 
  case 4:
    if(STOPBITS==2)
    {
      rtty_txbit (1); // Stop Bit
      txstatus=2;
      break;
    }
    else
    {
      txstatus=2;
      break;
    }

  }
}

void rtty_txbit (int bit)
{
  if (bit)
  {
    digitalWrite(MTX2_TXD,HIGH);
    //#ifdef APRS
//    analogWrite(MTX2_TXD, MTX2_OFFSET+((MTX2_SHIFT*4)/16)); // High
    //#endif
    //#ifndef APRS
    //    analogWrite(MTX2_TXD, MTX2_OFFSET+((MTX2_SHIFT*1.8)/16)); // High
    //#endif

  }
  else
  {
      digitalWrite(MTX2_TXD,LOW);
//    analogWrite(MTX2_TXD, MTX2_OFFSET); // Low
  }
}
void resetGPS() {
  uint8_t set_reset[] = {
    0xB5, 0x62, 0x06, 0x04, 0x04, 0x00, 0xFF, 0x87, 0x00, 0x00, 0x94, 0xF5           };
  sendUBX(set_reset, sizeof(set_reset)/sizeof(uint8_t));
}
void sendUBX(uint8_t *MSG, uint8_t len) {
  Serial.flush();
  Serial.write(0xFF);
  wait(100);
  for(int i=0; i<len; i++) {
    Serial.write(MSG[i]);
  }
}
void setupGPS() {
  // Turning off all GPS NMEA strings apart on the uBlox module
  // Taken from Project Swift (rather than the old way of sending ascii text)
  int gps_set_sucess=0;
  uint8_t setNMEAoff[] = {
    0xB5, 0x62, 0x06, 0x00, 0x14, 0x00, 0x01, 0x00, 0x00, 0x00, 0xD0, 0x08, 0x00, 0x00, 0x80, 0x25, 0x00, 0x00, 0x07, 0x00, 0x01, 0x00, 0x00, 0x00, 0x00, 0x00, 0xA0, 0xA9           };
  sendUBX(setNMEAoff, sizeof(setNMEAoff)/sizeof(uint8_t));
  while(!gps_set_sucess)
  {
    sendUBX(setNMEAoff, sizeof(setNMEAoff)/sizeof(uint8_t));
    gps_set_sucess=getUBX_ACK(setNMEAoff);
    if(!gps_set_sucess)
    {
      blinkled(2);
    }
  }
  wait(500);
  setGPS_GNSS();
  wait(500);
  setGPS_DynamicModel6();
  wait(500);
  setGps_MaxPerformanceMode();
  wait(500);
}

void setGPS_DynamicModel6()
{
  int gps_set_sucess=0;
  uint8_t setdm6[] = {
    0xB5, 0x62, 0x06, 0x24, 0x24, 0x00, 0xFF, 0xFF, 0x06,
    0x03, 0x00, 0x00, 0x00, 0x00, 0x10, 0x27, 0x00, 0x00,
    0x05, 0x00, 0xFA, 0x00, 0xFA, 0x00, 0x64, 0x00, 0x2C,
    0x01, 0x00, 0x00, 0x00, 0x00, 0x00, 0x00, 0x00, 0x00,
    0x00, 0x00, 0x00, 0x00, 0x00, 0x00, 0x16, 0xDC           };
  while(!gps_set_sucess)
  {
    sendUBX(setdm6, sizeof(setdm6)/sizeof(uint8_t));
    gps_set_sucess=getUBX_ACK(setdm6);
  }
}
void setGPS_GNSS()
{
  // Sets CFG-GNSS to disable everything other than GPS GNSS
  // solution. Failure to do this means GPS power saving 
  // doesn't work. Not needed for MAX7, needed for MAX8's
  int gps_set_sucess=0;
  uint8_t setgnss[] = {
    0xB5, 0x62, 0x06, 0x3E, 0x2C, 0x00, 0x00, 0x00,
    0x20, 0x05, 0x00, 0x08, 0x10, 0x00, 0x01, 0x00,
    0x01, 0x01, 0x01, 0x01, 0x03, 0x00, 0x00, 0x00,
    0x01, 0x01, 0x03, 0x08, 0x10, 0x00, 0x00, 0x00,
    0x01, 0x01, 0x05, 0x00, 0x03, 0x00, 0x00, 0x00,
    0x01, 0x01, 0x06, 0x08, 0x0E, 0x00, 0x00, 0x00,
    0x01, 0x01, 0xFC, 0x11   };
  while(!gps_set_sucess)
  {
    sendUBX(setgnss, sizeof(setgnss)/sizeof(uint8_t));
    gps_set_sucess=getUBX_ACK(setgnss);
  }
}
void setGPS_DynamicModel3()
{
  int gps_set_sucess=0;
  uint8_t setdm3[] = {
    0xB5, 0x62, 0x06, 0x24, 0x24, 0x00, 0xFF, 0xFF, 0x03,
    0x03, 0x00, 0x00, 0x00, 0x00, 0x10, 0x27, 0x00, 0x00,
    0x05, 0x00, 0xFA, 0x00, 0xFA, 0x00, 0x64, 0x00, 0x2C,
    0x01, 0x00, 0x00, 0x00, 0x00, 0x00, 0x00, 0x00, 0x00,
    0x00, 0x00, 0x00, 0x00, 0x00, 0x00, 0x13, 0x76           };
  while(!gps_set_sucess)
  {
    sendUBX(setdm3, sizeof(setdm3)/sizeof(uint8_t));
    gps_set_sucess=getUBX_ACK(setdm3);
  }
}
void setGps_MaxPerformanceMode() {
  //Set GPS for Max Performance Mode
  uint8_t setMax[] = { 
    0xB5, 0x62, 0x06, 0x11, 0x02, 0x00, 0x08, 0x00, 0x21, 0x91           }; // Setup for Max Power Mode
  sendUBX(setMax, sizeof(setMax)/sizeof(uint8_t));
}

boolean getUBX_ACK(uint8_t *MSG) {
  uint8_t b;
  uint8_t ackByteID = 0;
  uint8_t ackPacket[10];
  unsigned long startTime = millis();

  // Construct the expected ACK packet    
  ackPacket[0] = 0xB5;	// header
  ackPacket[1] = 0x62;	// header
  ackPacket[2] = 0x05;	// class
  ackPacket[3] = 0x01;	// id
  ackPacket[4] = 0x02;	// length
  ackPacket[5] = 0x00;
  ackPacket[6] = MSG[2];	// ACK class
  ackPacket[7] = MSG[3];	// ACK id
  ackPacket[8] = 0;		// CK_A
  ackPacket[9] = 0;		// CK_B

  // Calculate the checksums
  for (uint8_t ubxi=2; ubxi<8; ubxi++) {
    ackPacket[8] = ackPacket[8] + ackPacket[ubxi];
    ackPacket[9] = ackPacket[9] + ackPacket[8];
  }

  while (1) {

    // Test for success
    if (ackByteID > 9) {
      // All packets in order!
      return true;
    }

    // Timeout if no valid response in 3 seconds
    if (millis() - startTime > 3000) { 
      return false;
    }

    // Make sure data is available to read
    if (Serial.available()) {
      b = Serial.read();

      // Check that bytes arrive in sequence as per expected ACK packet
      if (b == ackPacket[ackByteID]) { 
        ackByteID++;
      } 
      else {
        ackByteID = 0;	// Reset and look again, invalid order
      }

    }
  }
}
uint16_t gps_CRC16_checksum (char *string)
{
  size_t i;
  uint16_t crc;
  uint8_t c;

  crc = 0xFFFF;

  // Calculate checksum ignoring the first two $s
  for (i = 5; i < strlen(string); i++)
  {
    c = string[i];
    crc = _crc_xmodem_update (crc, c);
  }

  return crc;
}

void blinkled(int blinks)
{
  for(int blinkledx = 0; blinkledx <= blinks; blinkledx++) {
    digitalWrite(LED_WARN,HIGH);
    wait(100);
    digitalWrite(LED_WARN,LOW);
    wait(100);
  }    
}    

void wait(unsigned long delaytime) // Arduino Delay doesn't get CPU Speeds below 8Mhz
{
  unsigned long _delaytime=millis();
  while((_delaytime+delaytime)>=millis()){
  }
}
uint8_t gps_check_nav(void)
{
  uint8_t request[8] = {
    0xB5, 0x62, 0x06, 0x24, 0x00, 0x00, 0x2A, 0x84           };
  sendUBX(request, 8);

  // Get the message back from the GPS
  gps_get_data();

  // Verify sync and header bytes
  if( buf[0] != 0xB5 || buf[1] != 0x62 ){
    GPSerror = 41;
  }
  if( buf[2] != 0x06 || buf[3] != 0x24 ){
    GPSerror = 42;
  }
  // Check 40 bytes of message checksum
  if( !_gps_verify_checksum(&buf[2], 40) ) {
    GPSerror = 43;
  }


  // Return the navigation mode and let the caller analyse it
  navmode = buf[8];
}
void gps_get_data()
{
  Serial.flush();
  // Clear buf[i]
  for(int i = 0;i<60;i++) 
  {
    buf[i] = 0; // clearing buffer  
  }  
  int i = 0;
  unsigned long startTime = millis();

  while ((i<60) && ((millis() - startTime) < 1000) ) { 
    if (Serial.available()) {
      buf[i] = Serial.read();
      i++;
    }
  }
}
bool _gps_verify_checksum(uint8_t* data, uint8_t len)
{
  uint8_t a, b;
  gps_ubx_checksum(data, len, &a, &b);
  if( a != *(data + len) || b != *(data + len + 1))
    return false;
  else
    return true;
}
void gps_ubx_checksum(uint8_t* data, uint8_t len, uint8_t* cka,
uint8_t* ckb)
{
  *cka = 0;
  *ckb = 0;
  for( uint8_t i = 0; i < len; i++ )
  {
    *cka += *data;
    *ckb += *cka;
    data++;
  }
}
void checkDynamicModel() {
  if(alt<=1000&&sats>4) {
    if(navmode != 3)
    {
      setGPS_DynamicModel3();
      errorstatus |=(1 << 3);  // Set Bit 3 indicating we are in pedestrian mode    
    }
  }
  else
  {
    if(navmode != 6){
      setGPS_DynamicModel6();
      errorstatus &= ~(1 << 3); // Unset bit 3 indicating we are in flight mode

    }
  }
}
void setGPS_PowerSaveMode() {
  // Power Save Mode 
  uint8_t setPSM[] = { 
    0xB5, 0x62, 0x06, 0x11, 0x02, 0x00, 0x08, 0x01, 0x22, 0x92           }; // Setup for Power Save Mode (Default Cyclic 1s)
  sendUBX(setPSM, sizeof(setPSM)/sizeof(uint8_t));
}
void prepare_data() {
  if(aprstxstatus==0)
  {
    sensors.requestTemperatures();
    temperature1=sensors.getTempCByIndex(0);
    if(tempsensors==2)
    {
      temperature2=sensors.getTempCByIndex(1);
    }
    if(temperature1==-127)
    {
      errorstatus |=(1 << 2); // Set bit 2 indicating the temp sensor is faulty
    }
    else
    {
      errorstatus &= ~(1 << 2); // Unset bit 2 indicating temp sensor is ok.
    }
  } 
  gps_check_lock();
  gps_get_position();
  gps_get_time();
  batteryadc_v=analogRead(BATTERY_ADC)*4.8;
  battvsmooth[4] = battvsmooth[3];
  battvsmooth[3] = battvsmooth[2];
  battvsmooth[2] = battvsmooth[1];
  battvsmooth[1] = battvsmooth[0];
  battvsmooth[0] = batteryadc_v;
  battvaverage = (battvsmooth[0]+battvsmooth[1]+ battvsmooth[2]+battvsmooth[3]+battvsmooth[4])/5;


}
void gps_check_lock()
{
  GPSerror = 0;
  Serial.flush();
  // Construct the request to the GPS
  uint8_t request[8] = {
    0xB5, 0x62, 0x01, 0x06, 0x00, 0x00,
    0x07, 0x16                                                                                                                                                                  };
  sendUBX(request, 8);

  // Get the message back from the GPS
  gps_get_data();
  // Verify the sync and header bits
  if( buf[0] != 0xB5 || buf[1] != 0x62 ) {
    GPSerror = 11;
  }
  if( buf[2] != 0x01 || buf[3] != 0x06 ) {
    GPSerror = 12;
  }

  // Check 60 bytes minus SYNC and CHECKSUM (4 bytes)
  if( !_gps_verify_checksum(&buf[2], 56) ) {
    GPSerror = 13;
  }

  if(GPSerror == 0){
    // Return the value if GPSfixOK is set in 'flags'
    if( buf[17] & 0x01 )
      lock = buf[16];
    else
      lock = 0;

    sats = buf[53];
  }
  else {
    lock = 0;
  }
}
void gps_get_position()
{
  GPSerror = 0;
  Serial.flush();
  // Request a NAV-POSLLH message from the GPS
  uint8_t request[8] = {
    0xB5, 0x62, 0x01, 0x02, 0x00, 0x00, 0x03, 0x0A           };
  sendUBX(request, 8);

  // Get the message back from the GPS
  gps_get_data();

  // Verify the sync and header bits
  if( buf[0] != 0xB5 || buf[1] != 0x62 )
    GPSerror = 21;
  if( buf[2] != 0x01 || buf[3] != 0x02 )
    GPSerror = 22;

  if( !_gps_verify_checksum(&buf[2], 32) ) {
    GPSerror = 23;
  }

  if(GPSerror == 0) {
    if(sats<4)
    {
      lat=0;
      lon=0;
      alt=0;
    }
    else
    {
      lon = (int32_t)buf[10] | (int32_t)buf[11] << 8 | 
        (int32_t)buf[12] << 16 | (int32_t)buf[13] << 24;
      lat = (int32_t)buf[14] | (int32_t)buf[15] << 8 | 
        (int32_t)buf[16] << 16 | (int32_t)buf[17] << 24;
      alt = (int32_t)buf[22] | (int32_t)buf[23] << 8 | 
        (int32_t)buf[24] << 16 | (int32_t)buf[25] << 24;
    }
    // 4 bytes of latitude/longitude (1e-7)
    lon_int=abs(lon/10000000);
    lon_dec=(labs(lon) % 10000000)/10;
    lat_int=abs(lat/10000000);
    lat_dec=(labs(lat) % 10000000)/10;


    // 4 bytes of altitude above MSL (mm)

    alt /= 1000; // Correct to meters
  }

}
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

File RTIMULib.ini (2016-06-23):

# #####################################################################
# 
# RTIMULib settings file

# General settings
# 

# IMU type - 
#   0 = Auto discover
#   1 = Null (used when data is provided from a remote IMU
#   2 = InvenSense MPU-9150
#   3 = STM L3GD20H + LSM303D
#   4 = STM L3GD20 + LSM303DLHC
#   5 = STM LSM9DS0
#   6 = STM LSM9DS1
#   7 = InvenSense MPU-9250
#   8 = STM L3GD20H + LSM303DLHC
#   9 = Bosch BMX055
#   10 = Bosch BNX055
IMUType=7

# 
# Fusion type type - 
#   0 - Null. Use if only sensor data required without fusion
#   1 - Kalman STATE4
#   2 - RTQF
FusionType=2

# 
# Is bus I2C: 'true' for I2C, 'false' for SPI
BusIsI2C=true

# 
# I2C Bus (between 0 and 7) 
I2CBus=1

# 
# SPI Bus (between 0 and 7) 
SPIBus=0

# 
# SPI select (between 0 and 1) 
SPISelect=0

# 
# SPI Speed in Hz
SPISpeed=500000

# 
# I2C slave address (filled in automatically by auto discover) 
I2CSlaveAddress=104

# 
# IMU axis rotation - see RTIMU.h for details
AxisRotation=0

# Pressure sensor type - 
#   0 = Auto discover
#   1 = Null (no hardware or don't use)
#   2 = BMP180
#   3 = LPS25H
#   4 = MS5611
#   5 = MS5637
PressureType=2

# 
# I2C pressure sensor address (filled in automatically by auto discover) 
I2CPressureAddress=119

# Humidity sensor type - 
#   0 = Auto discover
#   1 = Null (no hardware or don't use)
#   2 = HTS221
#   3 = HTU21D
HumidityType=0

# 
# I2C humidity sensor address (filled in automatically by auto discover) 
I2CHumidityAddress=0

# #####################################################################
# 

# Compass calibration settings
CompassCalValid=false
CompassCalMinX=0.000000
CompassCalMinY=0.000000
CompassCalMinZ=0.000000
CompassCalMaxX=0.000000
CompassCalMaxY=0.000000
CompassCalMaxZ=0.000000

# #####################################################################
# 

# Compass adjustment settings
# Compass declination is in radians and is subtracted from calculated heading
compassAdjDeclination=0.000000

# #####################################################################
# 

# Compass ellipsoid calibration
compassCalEllipsoidValid=false
compassCalOffsetX=0.000000
compassCalOffsetY=0.000000
compassCalOffsetZ=0.000000
compassCalCorr11=1.000000
compassCalCorr12=0.000000
compassCalCorr13=0.000000
compassCalCorr21=0.000000
compassCalCorr22=1.000000
compassCalCorr23=0.000000
compassCalCorr31=0.000000
compassCalCorr32=0.000000
compassCalCorr33=1.000000

# #####################################################################
# 

# Accel calibration
AccelCalValid=false
AccelCalMinX=0.000000
AccelCalMinY=0.000000
AccelCalMinZ=0.000000
AccelCalMaxX=0.000000
AccelCalMaxY=0.000000
AccelCalMaxZ=0.000000

# #####################################################################
# 

# Saved gyro bias data
GyroBiasValid=true
GyroBiasX=-0.022298
GyroBiasY=-0.026270
GyroBiasZ=0.015698

# #####################################################################
# 
# MPU-9150 settings
# 

# Gyro sample rate (between 5Hz and 1000Hz) 
MPU9150GyroAccelSampleRate=50

# 
# Compass sample rate (between 1Hz and 100Hz) 
MPU9150CompassSampleRate=25

# 
# Gyro/accel low pass filter - 
#   0 - gyro: 256Hz, accel: 260Hz
#   1 - gyro: 188Hz, accel: 184Hz
#   2 - gyro: 98Hz, accel: 98Hz
#   3 - gyro: 42Hz, accel: 44Hz
#   4 - gyro: 20Hz, accel: 21Hz
#   5 - gyro: 10Hz, accel: 10Hz
#   6 - gyro: 5Hz, accel: 5Hz
MPU9150GyroAccelLpf=4

# 
# Gyro full scale range - 
#   0  - +/- 250 degress per second
#   8  - +/- 500 degress per second
#   16 - +/- 1000 degress per second
#   24 - +/- 2000 degress per second
MPU9150GyroFSR=16

# 
# Accel full scale range - 
#   0  - +/- 2g
#   8  - +/- 4g
#   16 - +/- 8g
#   24 - +/- 16g
MPU9150AccelFSR=16

# #####################################################################
# 
# MPU-9250 settings
# 

# Gyro sample rate (between 5Hz and 1000Hz plus 8000Hz and 32000Hz) 
MPU9250GyroAccelSampleRate=80

# 
# Compass sample rate (between 1Hz and 100Hz) 
MPU9250CompassSampleRate=40

# 
# Gyro low pass filter - 
#   0x11 - 8800Hz, 0.64mS delay
#   0x10 - 3600Hz, 0.11mS delay
#   0x00 - 250Hz, 0.97mS delay
#   0x01 - 184Hz, 2.9mS delay
#   0x02 - 92Hz, 3.9mS delay
#   0x03 - 41Hz, 5.9mS delay
#   0x04 - 20Hz, 9.9mS delay
#   0x05 - 10Hz, 17.85mS delay
#   0x06 - 5Hz, 33.48mS delay
MPU9250GyroLpf=3

# 
# Accel low pass filter - 
#   0x08 - 1130Hz, 0.75mS delay
#   0x00 - 460Hz, 1.94mS delay
#   0x01 - 184Hz, 5.80mS delay
#   0x02 - 92Hz, 7.80mS delay
#   0x03 - 41Hz, 11.80mS delay
#   0x04 - 20Hz, 19.80mS delay
#   0x05 - 10Hz, 35.70mS delay
#   0x06 - 5Hz, 66.96mS delay
MPU9250AccelLpf=3

# 
# Gyro full scale range - 
#   0  - +/- 250 degress per second
#   8  - +/- 500 degress per second
#   16 - +/- 1000 degress per second
#   24 - +/- 2000 degress per second
MPU9250GyroFSR=16

# 
# Accel full scale range - 
#   0  - +/- 2g
#   8  - +/- 4g
#   16 - +/- 8g
#   24 - +/- 16g
MPU9250AccelFSR=16
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

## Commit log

2016-05-14 Reviewed BoM in excel format for procurement
    [BoM.xlsx]
2016-05-16 Updated with Balloon insuflator link
    [BoM.xlsx]
2016-05-20 altitude+pressão e ini file para definir Pythonpath
2016-06-01 Added Arduberry
    [BoM.xlsx]
2016-06-03 Collecting data from the 2 grove sensors
2016-06-03 Updated after reception of first batch of material
    [BoM.xlsx]
2016-06-06 renamed some files for consistency, fixed path of GrovePi dependency in the sensors script, added script-dependencies.txt to help with setting up the scripts
    [RTIMULib.ini]
2016-06-06 issue #25 - pesos dos vários materiais
    [pesos.xlsx]
2016-06-06 scripts are set as executable, added shebang to the sensors script. We can run these as ./scriptname.py
2016-06-06 Updated balloon and parachute for procurement
    [BoM.xlsx]
2016-06-23 fixed date formatting for filenames of pics/vids; ignoring exceptions when getting sensor data, in hope the script can continue executing;
    [RTIMULib.ini]
2016-06-23 tweaked camera parameters for sun exposure
2016-06-26 ppt com a info tag para a payload
2016-06-30 docs and logo updates
    [RELEVO.stl, RELEVO2.stl, VAZADO.stl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]
2016-07-01 updated with radio checks and raspberry pi clock setup before script execution
2016-07-02 added ground stations materials

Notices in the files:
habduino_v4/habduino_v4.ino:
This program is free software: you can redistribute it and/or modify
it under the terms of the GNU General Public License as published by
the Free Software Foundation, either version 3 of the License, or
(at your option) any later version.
